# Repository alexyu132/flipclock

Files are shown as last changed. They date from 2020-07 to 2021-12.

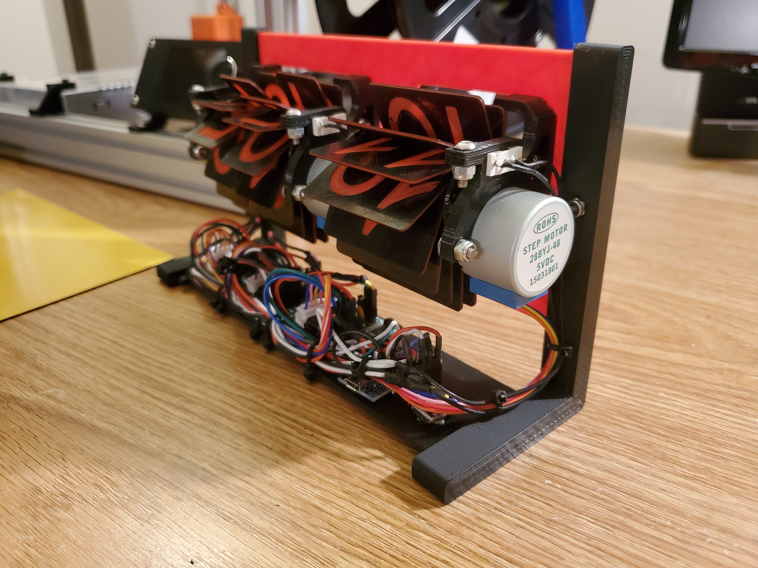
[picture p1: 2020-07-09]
images/2.jpg

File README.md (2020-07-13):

# Flipclock
Arduino-powered clock using split-flap mechanical displays.

https://www.youtube.com/watch?v=v2_D-W6b9TM

Flip clock image
Flip clock image
## Features
- Automatic time setting on sketch upload
- RTC module keeps track of time even when unpowered
- US DST support - clock automatically skips forward/back 1 hour as needed
- Runs off of Arduino's USB power - no separate power input needed
- Automatic calibration once per rotation using mechanical endstops
- Steppers turned off when not moving for power savings
- Endstop failure detection - shuts down if homing takes over 2 full rotations

# Non-printed parts
|  Part | Quantity | Notes  |
|---|---|---|
|  M3x10mm button head bolt | 19  | |
|  M3 lock nut | 19 | |
| 28byj-48 stepper motor | 3 | |
| ULN2003 stepper driver | 3 | |
| Pro Micro or similar small Arduino (5V) | 1 |
| DS3231 RTC module | 1 |
| PCB endstop | 3 | Will need to cut the switches off and solder leads to the C and NO pins |
| Zip ties | Varies | |
| Wires (22AWG or similar) | Varies | |
| Double-sided tape | Varies | |

# Printing
The parts are designed to print without supports. Recommended layer height is 0.2mm or lower.

The numbers on the flaps are inset by 0.2mm, so these parts are recommended to be printed at a 0.2mm height. If you don't want to color in the numbers manually, you can pause the print after the first layer and swap to a different filament color. Make sure to pause before the last layer to swap the original color back in.

# Assembly
## Displays
1. Use 2 M3x10mm bolts and lock nuts to attach a motor to the motor mount.
1. Install the rotor end cap onto the motor shaft, with the protruding nub facing the motor body.
1. Press the rotor onto the motor shaft. The rotor should interlock with the rotor end cap.
1. Snap the flaps onto the rotor. If having trouble attaching the flaps, it may help to slightly back the rotor off the shaft for a bit more clearance. The top halves of the display should be the side that was facedown on the print bed, and the opposite should be true for the bottom halves. If installed correctly, the numbers should count up when the display turns. (Note: the tens display (the one in the middle) has 2 identical sets of numbers. For 1 rotation of the display, it should count from 0 to 5 twice.)
1. If you haven't already, cut the switch off of each endstop circuit board and solder leads to the C and NO pins.
1. Slip the endstop switch through the rectangular cutout above the motor. The switch can be moved forward and backward to control how close it is to the rotor end cap. Adjust the switch position so that the nub on the end cap triggers the switch. Lock the switch in position with another M3x10mm bolt and lock nut.

## Frame
1. Attach each display to the faceplate using 2 bolts and lock nuts each.
1. Attach the stand pieces to the sides of the faceplate and electronics tray. Use bolts and lock nuts to secure everything in place (4 total).

## Electronics
1. To make cable management easier, the faceplate and stand pieces have zip tie attachment points. The hours display cables should be routed by the left stand, and the other displays should be routed towards the right stand. Due to the length of the stepper motor cables, it is cleaner to wire the stepper drivers in the opposite order of the displays, i.e. the rightmost driver is attached to the leftmost display.
1. The stepper drivers attach with zip ties. At first, only attach the zip ties near the front of the clock, as the rear zip ties will also be used for cable management.
1. Wire the RTC module to the I2C pins on the Arduino. On the Pro Micro, connect SDA to pin 2 and SCL to pin 3. Ground and VCC on the RTC should be wired to the corresponding pins on the Arduino.
1. Wire the 5V and ground pins of the stepper driver to the VCC and ground pins, respectively, on the Arduino.
1. Wire the steppers to the Arduino. On the Pro Micro, the recommended pins are 4, 5, 6, 7 for the hours display; 8, 9, 10, 16 for the tens display; and 14, 15, A0, A1 for the ones display.
1. Wire one side of each endstop to ground on the Arduino, and the other side to an IO pin. On the Pro Micro, it's recommended to connect the hour endstop to A3, the tens endstop to A2, and the ones endstop to TX0 (digital 1). If you want to keep the TX/RX pins free for something else, the endstops for the tens and ones displays can be wired together and share the A2 pin.
1. After everything is wired up, use double sided tape to stick the Arduino and RTC module to the electronics tray.
1. Use zip ties through the rear stepper driver holes to secure the cables.

# Calibration and operation
The driver code is provided in the 'flipclock' folder. The configurable parameters, as well as their descriptions, are at the top of the file. Edit these as needed. When uploading the sketch, be ready to quickly unplug the clock if any of the displays are turning backwards, as this could damage the endstop switches. If a display turns backwards, reverse the order of the pins for that display in the sketch file.

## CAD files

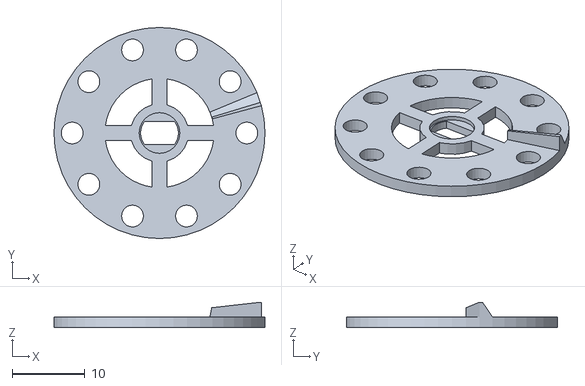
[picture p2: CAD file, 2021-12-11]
stl/cap_ones.stl
29.0 x 29.0 x 3.50

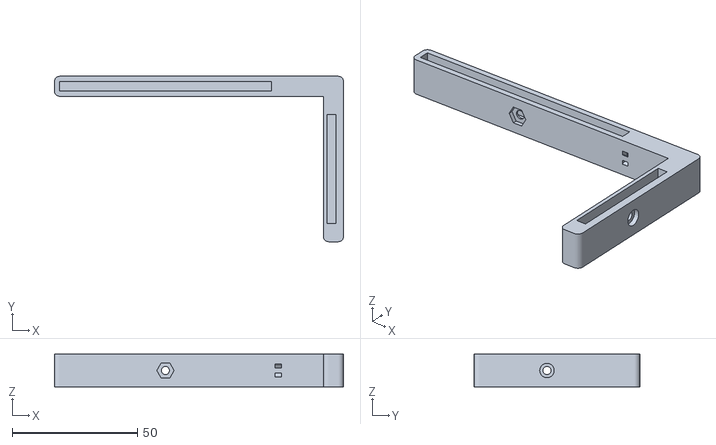
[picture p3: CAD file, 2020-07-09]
stl/stand_right.stl
115.2 x 66.0 x 13.0

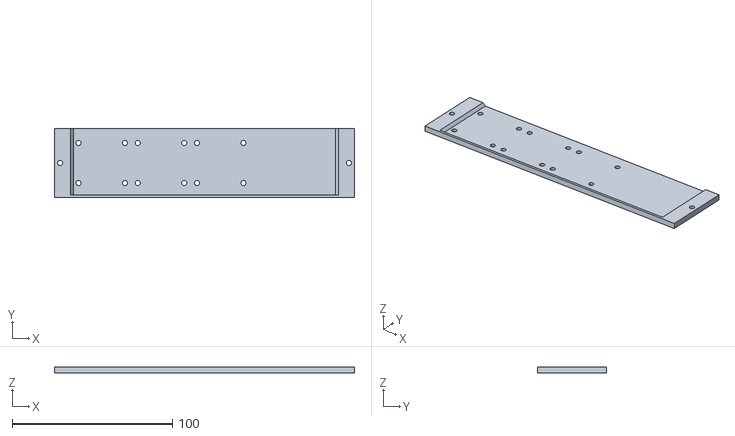
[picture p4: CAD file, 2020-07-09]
stl/electronics_mount.stl
187.3 x 43.0 x 3.50

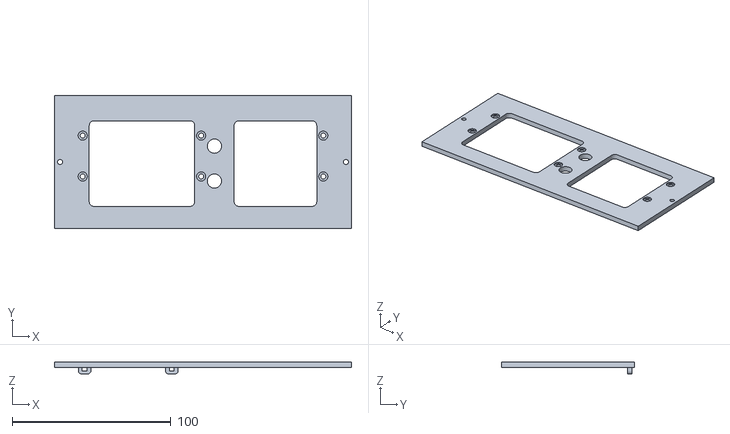
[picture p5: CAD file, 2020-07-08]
stl/faceplate.stl
187.3 x 84.0 x 7.50

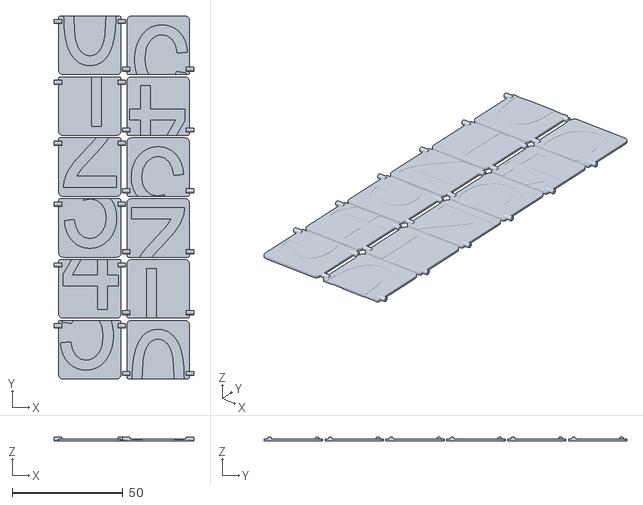
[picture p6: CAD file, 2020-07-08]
stl/flaps_tens.stl
63.1 x 164.0 x 2.02

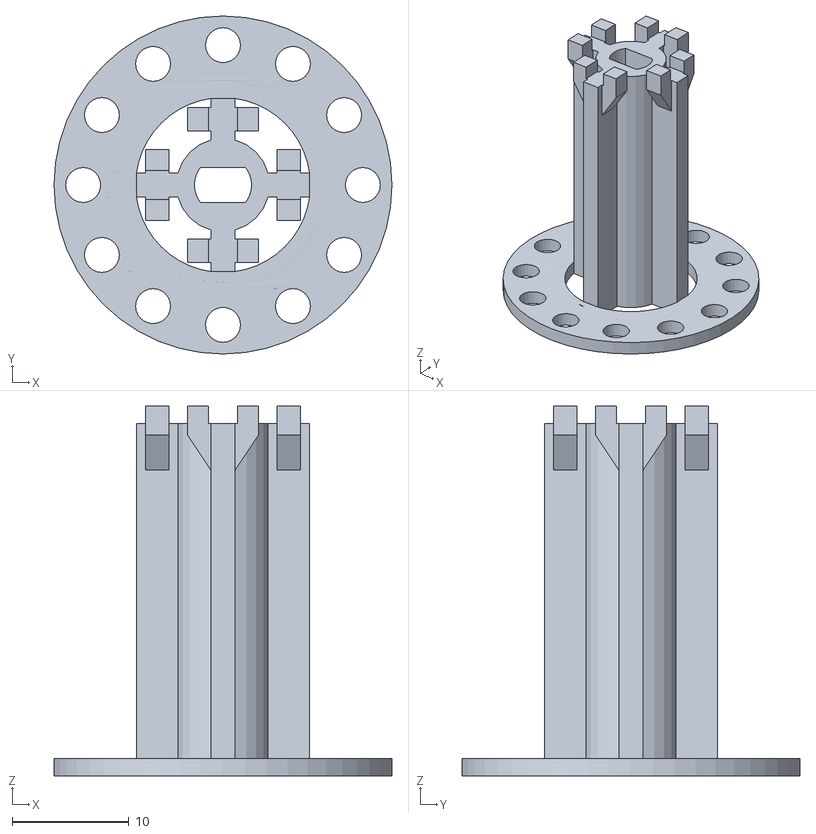
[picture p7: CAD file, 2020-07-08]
stl/rotor_tens.stl
29.0 x 29.0 x 31.8

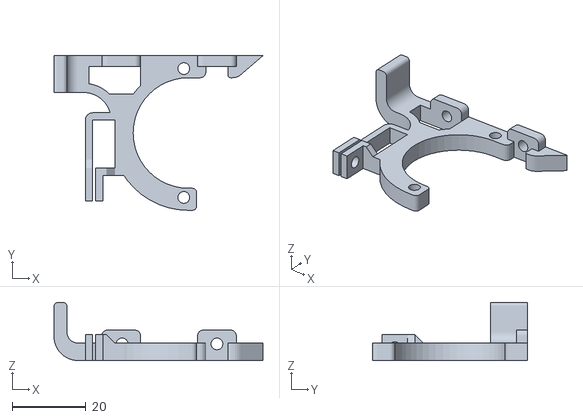
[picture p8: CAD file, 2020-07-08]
stl/motor_mount_ones.stl
56.8 x 42.0 x 15.8

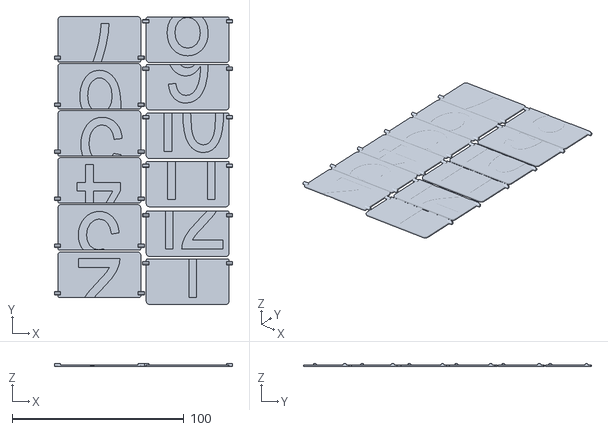
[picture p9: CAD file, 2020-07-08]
stl/flaps_hour.stl
103.6 x 167.5 x 2.02

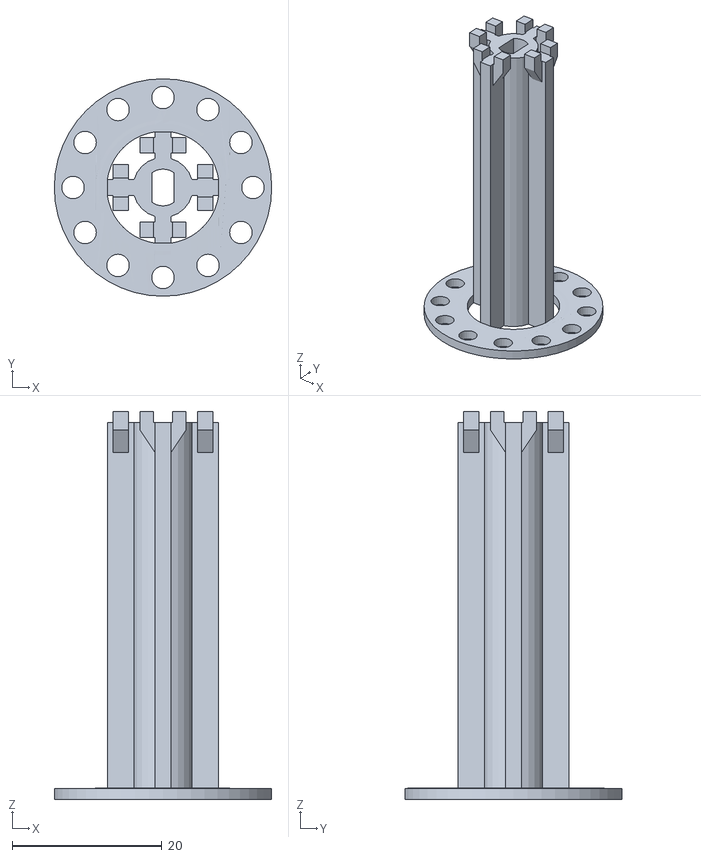
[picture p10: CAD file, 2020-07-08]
stl/rotor_hour.stl
29.0 x 29.0 x 51.8

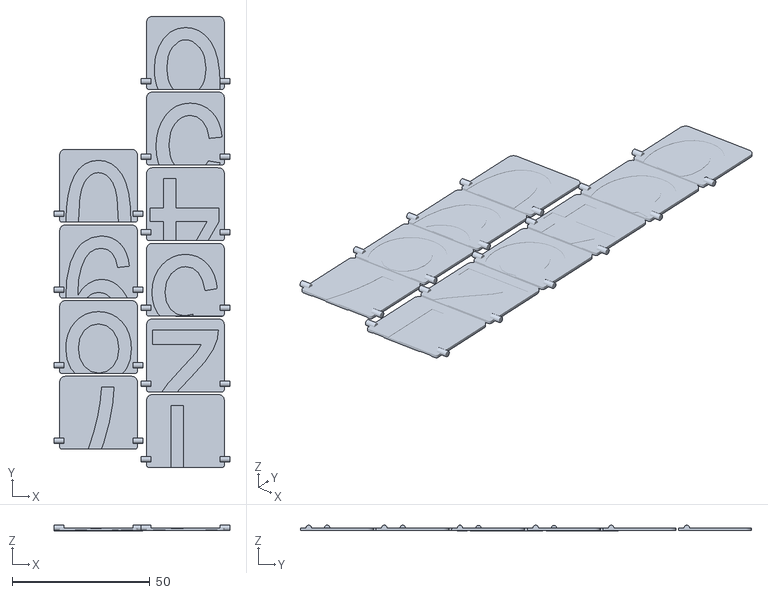
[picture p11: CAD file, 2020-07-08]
stl/flaps_ones.stl
63.9 x 164.0 x 2.14

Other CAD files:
stl/stand_left.stl
stl/rotor_ones.stl
stl/cap_tens_hour.stl
stl/motor_mount_hour_tens.stl

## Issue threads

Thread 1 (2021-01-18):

Flaps_ones.stl

brettoliver, 2021-01-18:
Hi thanks for sharing this clock.
I am having probles printing 2 colours on Flaps_ones.stl.
In Cura I add a pause at selected layers to change filament.
On Flaps tens and hour I can pause the print at layer 1 to change filament. On Flaps_ones.stl layer 1 only includes a few flaps. layer 2 includes all flaps but also prints over the few flaps printed in layer 1.
This means I am unable to print flaps_ones in 2 colours.

Is there a way around this?

Layer 1
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

Layer 2
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

brettoliver, 2021-01-27:
Update - I have got around this issue by splitting the "flapones" file and taking out 3 flaps. I then print it as 2 seperate files. I use a Pause at height script in Cura to stop the printer automatically when changing fillament colours.

Closed 2021-01-27.

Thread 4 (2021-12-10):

Holes for flaps of ones slightly off

timminator93, 2021-12-10:
Tthe holes of Cap ones and rotor ones don´t match exactly. So the display is a bit diagonal.

alexyu132, 2021-12-11:
Fixed, thanks for catching

Closed 2021-12-11.

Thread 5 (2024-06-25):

3D files wrong

Hrei2, 2024-06-25:
At least the ones are wrong. You have to cut off like 0.05 mm from the bottom for it to work.

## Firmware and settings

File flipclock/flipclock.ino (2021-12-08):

// Flip clock driver code
// Automatically sets time on compile, supports US DST
// Requires Adafruit RTCLib to be installed

#include "RTClib.h"

// ----------- BEGIN CONFIGURABLE SECTION -----------



// Half steps needed for the motors to perform a single rotation.
// Usually 4096 for 28byj-48 steppers
#define STEPS_PER_REV 4096

// The default delay after each motor step in microseconds. 
// Adjusts the speed of the displays. Higher value = slower
#define STEPPER_DELAY 1400

// Comment out the following line to disable DST support if EU DST is used set your time zone
#define USE_DST_US
//#define USE_DST_EU
//Timezone for EU
#define timeZone 1

// Adjust this to the time in seconds it takes to compile and upload to the Arduino
// If the clock runs slow by a few seconds, increase this value, and vice versa. Value cannot be negative.
#define UPLOAD_OFFSET 5

// Delay amount in ms added to the end of each loop iteration.
// Some people have reported that reading the RTC time too often causes timing issues, so this value reduces the polling frequency.
#define POLLING_DELAY 50

// Number of repeated endstop reads during homing. Must be positive.
// Leave this value alone unless homing is unreliable.
#define ENDSTOP_DEBOUNCE_READS 3

// Stepper pin definitions
// 1st row - Hours
// 2nd row - Minutes (Tens)
// 3rd row - Minutes (Ones)
// If a display is turning backwards, reverse the order of the pins for that display.
const byte stepper_pins[][4] = { {7, 6, 5, 4},
                               {16, 10, 9, 8},
                               {14, 15, 18, 19} };

// Endstop pin definitions
// The endstops for the tens and ones displays can be wired together and share a pin if needed.
// This is necessary on the Pro Micro if you want to use the TX/RX pins for something else.
// Same order as before: Hours, Minutes (Tens), Minutes (Ones)
const byte endstop_pins[] = {21,20,20};

// LED pin - flashes slowly when an error is detected, powered off otherwise. Can comment out to disable this functionality.
// On the Pro Micro, pin 30 is the TX LED.
#define LED_PIN 30
// Set this to true if a high signal turns off the LED.
#define LED_INVERT true

// On the Pro Micro, the RX LED is lit by default (annoying) and should be manually turned off.
// Comment out the following 2 lines if your board doesn't have a second controllable LED.
#define LED_2_PIN 17
#define LED_2_INVERT true

// Homing settings - modify these to calibrate your displays

// Set these to the number that is displayed after the endstop is triggered.
// Note: If the starting digit for the hours display is 12, enter 0 below.
const byte starting_digits[] = {0, 0, 9};

// The following parameter configures how much the stepper turns after homing.
// Starting offset should be increased until the top flap touches the front stop.
const unsigned int starting_offset[] = {110, 80, 265};

// ----------- END CONFIGURABLE SECTION -----------

// Position in steps of each stepper (relative to homing point)
unsigned int stepper_pos[] = {0,0,0};

// Current drive step for each stepper - 0 to 7 for half-stepping
byte drive_step[] = {0, 0, 0};

RTC_DS3231 rtc;

#if defined(USE_DST_US)
  unsigned int year_old = 0;
  DateTime dst_start, dst_end;
#endif

// Stops the program. Flashes LED slowly if LED pin is defined.
void e_stop() {
  #if defined(LED_PIN)
    while(1) {
      digitalWrite(LED_PIN, HIGH);
      delay(1000);
      digitalWrite(LED_PIN, LOW);
      delay(1000);
    }
  #else
    abort();
  #endif
}

void disable_stepper(const byte stepper_num) {
  digitalWrite(stepper_pins[stepper_num][0], LOW);
  digitalWrite(stepper_pins[stepper_num][1], LOW);
  digitalWrite(stepper_pins[stepper_num][2], LOW);
  digitalWrite(stepper_pins[stepper_num][3], LOW);
}

void half_step(const byte stepper_num) {
  const byte pos = drive_step[stepper_num];
  digitalWrite(stepper_pins[stepper_num][0], pos < 3);
  digitalWrite(stepper_pins[stepper_num][1], ((pos + 6) % 8) < 3);
  digitalWrite(stepper_pins[stepper_num][2], ((pos + 4) % 8) < 3);
  digitalWrite(stepper_pins[stepper_num][3], ((pos + 2) % 8) < 3);
  drive_step[stepper_num] = (pos + 1) % 8;
}

// Take the specified amount of steps for a stepper connected to the specified pins, with a
// specified delay (in microseconds) between each step.
void step_num(const byte stepper_num, unsigned int steps, const unsigned int wait) {
  stepper_pos[stepper_num] = (stepper_pos[stepper_num] + steps) % STEPS_PER_REV;
  while(steps > 0) {
    half_step(stepper_num);
    steps--;  
    delayMicroseconds(wait);
  }
}

// Step until the endstop is pressed and released, and update the stepper position to 0.
// If homing doesn't end after 2 rotations, the endstop is assumed to have failed and the program aborts.
void step_to_home(const byte stepper_num, const unsigned int wait) {  
  unsigned int total_steps = 0;
  byte endstop_repeats = 0;
  
  // Step until endstop reads low ENDSTOP_DEBOUNCE_READS times in a row
  while(endstop_repeats < ENDSTOP_DEBOUNCE_READS) {
    endstop_repeats = digitalRead(endstop_pins[stepper_num]) == LOW ? endstop_repeats + 1 : 0;
    
    half_step(stepper_num);    
    total_steps++;
    if(total_steps > STEPS_PER_REV * 2u) {
      disable_stepper(stepper_num);
      e_stop();
    } 
    delayMicroseconds(wait);
  }
  endstop_repeats = 0;
  
  // Step until endstop reads high ENDSTOP_DEBOUNCE_READS times in a row
  while(endstop_repeats < ENDSTOP_DEBOUNCE_READS) {
    endstop_repeats = digitalRead(endstop_pins[stepper_num]) == HIGH ? endstop_repeats + 1 : 0;
    
    half_step(stepper_num);
    total_steps++;
    if(total_steps > STEPS_PER_REV * 2u) {
      disable_stepper(stepper_num);
      e_stop();
    }
    delayMicroseconds(wait);
  }

  stepper_pos[stepper_num] = 0; 
}

// Step to the specified position. If the current position is greater than the target position, this
// function will re-home and then step to the target position.
void step_to_position(const byte stepper_num, unsigned int target_pos, const unsigned int wait) {
  if (target_pos == stepper_pos[stepper_num]) {
    return;
  }

  // Limit target position to between 0 and STEPS_PER_REV-1
  target_pos %= STEPS_PER_REV;
  
  if (target_pos < stepper_pos[stepper_num]) {
    step_to_home(stepper_num, wait);
    step_num(stepper_num, target_pos, wait);
  } else {
    step_num(stepper_num, target_pos - stepper_pos[stepper_num], wait);
  }
}

// Steps to the specified digit on the display
// To save power, stepper is powered off after running, so exact positional accuracy is not maintained.
// This is allowable since the displays self-calibrate via the endstops every rotation.
void step_to_digit(const byte stepper_num, const byte digit, const unsigned int wait) {
  // The ones display has 10 flaps, the others have 12 flaps
  const byte num_flaps = (stepper_num == 2) ? 10 : 12;
  
  const byte num_digits = (stepper_num == 0) ? 12 : (stepper_num == 1) ? 6 : 10;

  const unsigned int target_pos = starting_offset[stepper_num] + (unsigned int)((num_digits + digit - starting_digits[stepper_num]) % num_digits) * STEPS_PER_REV/num_flaps;
  
  // The tens display has 2 full sets of digits, so we'll need to step to the closest target digit.
  if(stepper_num == 1) {
    // The repeated digit is offset by a half-rotation from the first target.
    const unsigned int second_target = target_pos + STEPS_PER_REV/2;

    // If the current position is between the two target positions, step to the second target position, as it's the closest given that we can't step backwards.
    // Otherwise, step to the first target position.
    if(stepper_pos[stepper_num] > target_pos && stepper_pos[stepper_num] <= second_target) {
      step_to_position(stepper_num, second_target, wait);
    } else {
      step_to_position(stepper_num, target_pos, wait);
    }
  } else {
    // The ones and hour displays only have a single set of digits, so simply step to the target position.
    step_to_position(stepper_num, target_pos, wait);
  }
  
  disable_stepper(stepper_num);
}

bool DST_EU(int year, int month, int day, int hour)
      {
      // There is no DST in Jan, Feb, Nov, Dec
      if(month < 3 || month > 10)
      { 
      return false;
      }
      //There is always DST in Apr, May, Jun, Jul, Aug, Sep
      if(month > 3 && month < 10)
      { 
      return true;
      }
      //Determin if its summertime accoridng to the European normation
      if(month == 3&&(hour+24*day)>=(1+timeZone+24*(31-(5*year/4+4)%7)) || month==10&&(hour+24*day)<(1+timeZone+24*(31-(5*year/4+1)%7)))
      { 
      return true;
      }
      
      else
      {
      return false;
      }
      }

void setup () {
  // Setting stepper pins to output
  for (byte i = 0; i < 3; i++) {
    for (byte j = 0; j < 4; j++) {
      pinMode(stepper_pins[i][j], OUTPUT);
    }
  }
  
  // Set endstop pins as input with pullups enabled
  pinMode(endstop_pins[0], INPUT_PULLUP);
  pinMode(endstop_pins[1], INPUT_PULLUP);
  pinMode(endstop_pins[2], INPUT_PULLUP);

  // Set LED pin to output and power it off
  #if defined(LED_PIN)
    pinMode(LED_PIN, OUTPUT);
    digitalWrite(LED_PIN, LED_INVERT);
  #endif

  // Turn off the second LED if needed
  #if defined(LED_2_PIN)
    pinMode(LED_2_PIN, OUTPUT);
    digitalWrite(LED_2_PIN, LED_2_INVERT);
  #endif

  if (!rtc.begin()) {
    e_stop();
  }

  if (rtc.lostPower()) {
    // Set the time to the compile time + offset
    DateTime compile_time = DateTime(F(__DATE__), F(__TIME__)) + TimeSpan(UPLOAD_OFFSET);
    
    #if defined(USE_DST_US)
      // Checking if compile time is in DST
      uint16_t year = compile_time.year();



//      //DST for US      
//      // DST starts on the second Sunday of March, 2AM
//      // Get beginning of second week and then offset to Sunday
      DateTime dst_start = DateTime(year, 3, 8, 2, 0, 0);
      dst_start = dst_start + TimeSpan((7-dst_start.dayOfTheWeek()) % 7, 0, 0, 0);
//    
//      // DST ends on the first Sunday of November, 2AM
//      // Get first day of month and then offset to Sunday
      DateTime dst_end = DateTime(year, 11, 1, 2, 0, 0);
      dst_end = dst_end + TimeSpan((7-dst_end.dayOfTheWeek()) % 7, 0, 0, 0);
//    
//      // If compile time is between DST start and end, then subtract 1 hour to get standard time
      compile_time = compile_time >= dst_start && compile_time < dst_end ? (compile_time - TimeSpan(0,1,0,0)) : compile_time;
    #endif

    #if defined(USE_DST_EU)
    
      if(DST_EU(compile_time.year(), compile_time.month(), compile_time.day(), compile_time.hour()))
      {
      compile_time = compile_time - TimeSpan(0,1,0,0);  
      }

    #endif
    
    rtc.adjust(compile_time);
  }
  
  // If the minute displays share an endstop pin (necessary on the Pro Micro), we need to make sure both of their endstops are unpressed before homing.
  // We can do this by alternatingly stepping each display in small increments until the endstop pin reads high.
  unsigned int total_steps = 0;
  if(endstop_pins[1] == endstop_pins[2]) {
    while(digitalRead(endstop_pins[1]) == LOW) {
      step_num(1, 200, STEPPER_DELAY);
      disable_stepper(1);

      // Still pressed, try the other display
      if(digitalRead(endstop_pins[1]) == LOW) {
        step_num(2, 200, STEPPER_DELAY);  
        disable_stepper(2);
      }

      // Similar to homing, if a max number of steps is reached, the endstop is assumed to have failed and the program aborts.
      total_steps += 200;
      if(total_steps > STEPS_PER_REV) {
        e_stop();
      }
    }
  }

  // Step to home digit
  step_to_home(2, STEPPER_DELAY);
  step_to_digit(2, starting_digits[2], STEPPER_DELAY);
  step_to_home(1, STEPPER_DELAY);
  step_to_digit(1, starting_digits[1], STEPPER_DELAY);
  step_to_home(0, STEPPER_DELAY);
  step_to_digit(0, starting_digits[0], STEPPER_DELAY);
}

void loop () {
  
  DateTime now = rtc.now();
  byte hr = now.hour() % 12;
  byte tens = now.minute() / 10;
  byte ones = now.minute() % 10;
  
  #if defined(USE_DST_US)
    // Calculate new DST cutoffs if the year changes
    if(now.year() != year_old) {
      // DST starts on the second Sunday of March, 2AM
      dst_start = DateTime(now.year(), 3, 8, 2, 0, 0);
      dst_start = dst_start + TimeSpan((7-dst_start.dayOfTheWeek()) % 7, 0, 0, 0);
    
      // DST ends on the first Sunday of November, 1AM (standard time)
      dst_end = DateTime(now.year(), 11, 1, 1, 0, 0);
      dst_end = dst_end + TimeSpan((7-dst_end.dayOfTheWeek()) % 7, 0, 0, 0); 
      
      year_old = now.year();
    }
    
    // If current time is between the DST cutoffs, add 1 to the hour digit
    hr = (now >= dst_start && now < dst_end) ? (hr + 1) % 12 : hr;
  #endif

      #if defined(USE_DST_EU)

      //DST for EU
      if(DST_EU(now.year(), now.month(), now.day(), now.hour()))
      {
      hr = now.hour() + 1;  
      }

    #endif

  
  
  step_to_digit(2, ones, STEPPER_DELAY);
  step_to_digit(1, tens, STEPPER_DELAY);
  step_to_digit(0, hr, STEPPER_DELAY);

  delay(POLLING_DELAY);
}

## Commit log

2020-07-07 Adjust endstop nub on ones display
2020-07-08 Remove trailing slope on endstop nubs
2020-07-08 tighten motor shaft clearances
2020-07-08 Add stls
    [cap_ones.stl, cap_tens_hour.stl, electronics_mount.stl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]
2020-07-09 Add error LED functionality
    [flipclock.ino]
2020-07-09 Bolted connection for stand pieces and electronics tray
    [electronics_mount.stl, stand_left.stl, stand_right.stl]
2020-07-09 Update endstop pin recommendations
2020-07-09 Make half step function more concise, turn off RX LED on Pro Micro
2020-07-09 Fix typo in LED code
    [flipclock.ino]
2021-12-04 Update flipclock.ino
    I added a support for auto DST in the EU.
    [flipclock.ino]
2021-12-11 Fix cap_ones hole alignment
    [cap_ones.stl]
